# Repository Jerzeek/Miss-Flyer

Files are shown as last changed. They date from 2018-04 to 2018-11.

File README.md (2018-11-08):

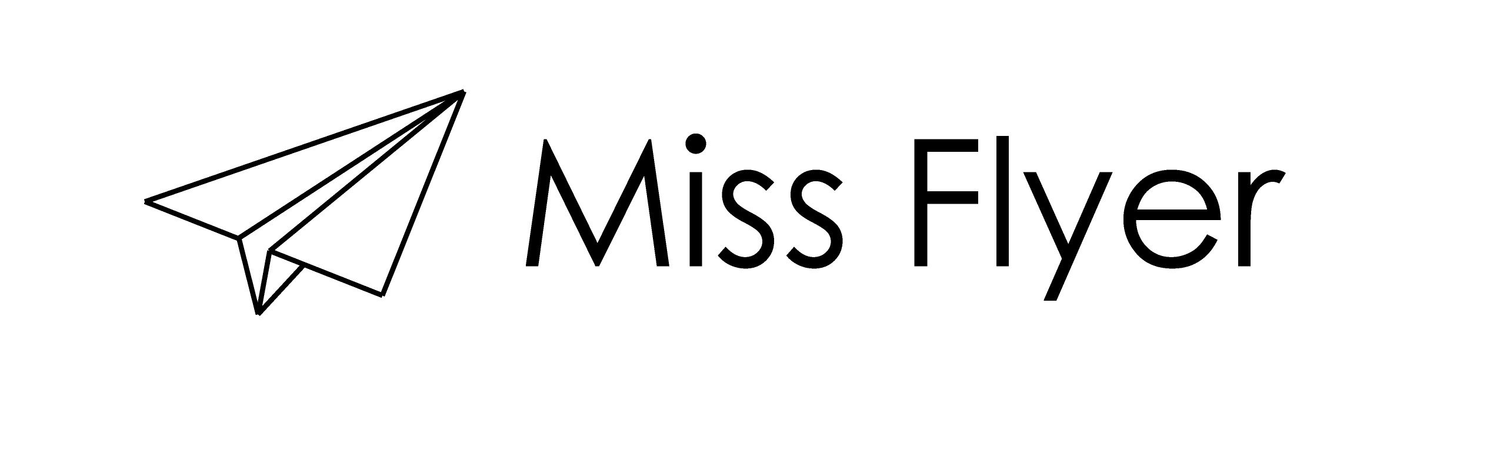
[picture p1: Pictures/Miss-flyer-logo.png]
Project logo

***
Miss Flyer the best use of a misprint!
It can turn an ordenairy paper into an extra ordaniary paper plane with only one swipe! :open_mouth:

Entirely made from one single sheet of lasercutted plywood.

KRO-NCRV, Klaas vindt uit (Dutch TV) seemed to like it, so they wanted to show it to everyone :smiley:
here is a to the video:
(click on image)
Klaas vindt uit video (https://www.youtube.com/watch?v=qRwEvvZekd8)

One gif says more than 1000 words:
Gif

Miss Flyer in use:
Demo photo

Overview photo:
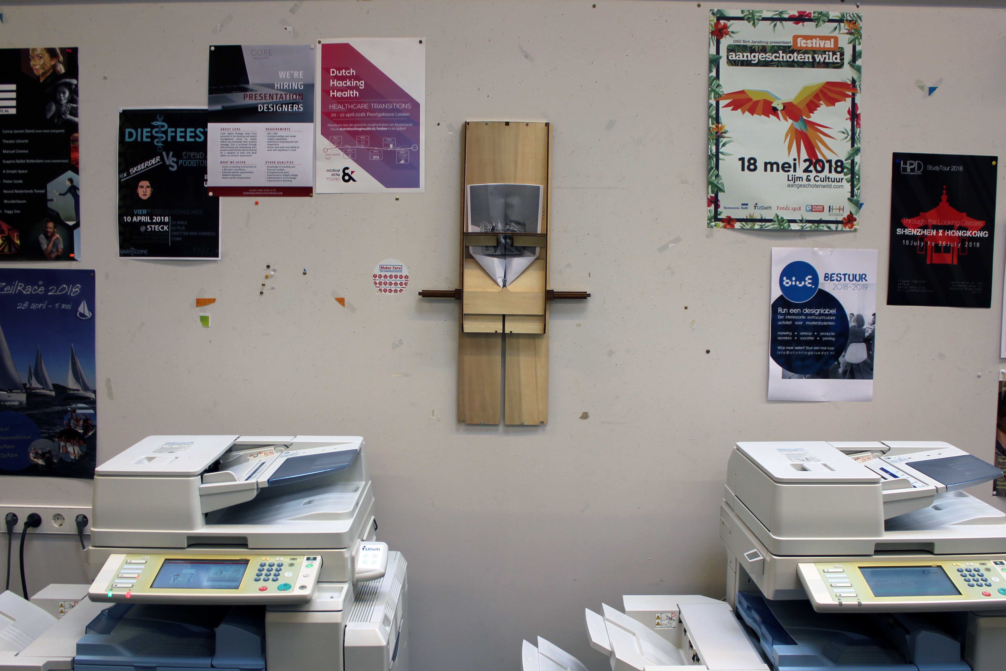
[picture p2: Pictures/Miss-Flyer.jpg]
overview


Lasercut overview:
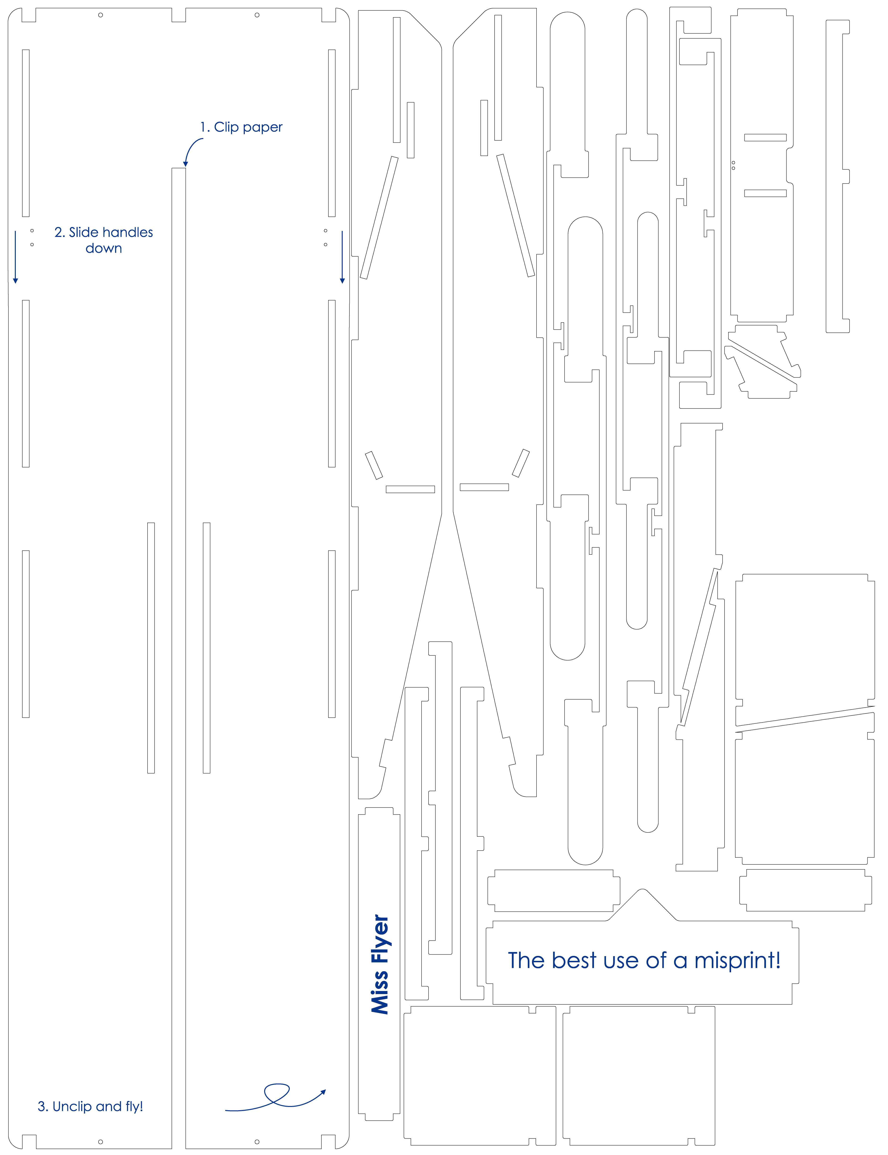
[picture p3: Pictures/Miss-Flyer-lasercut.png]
Lasercut photo


Initial sketch:
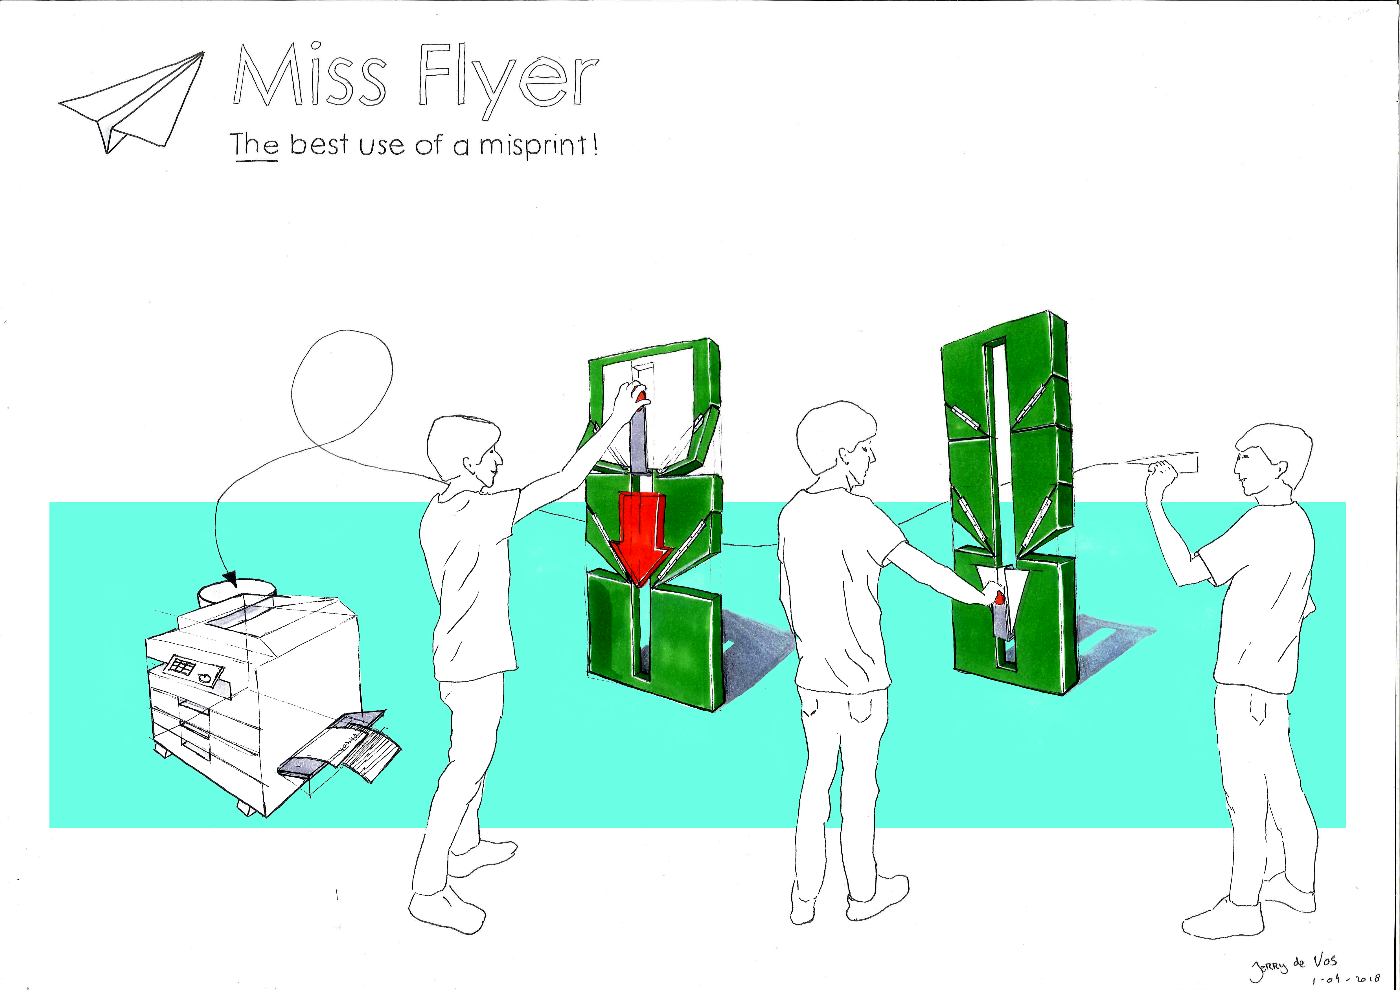
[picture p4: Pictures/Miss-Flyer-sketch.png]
Initial sketch


How i made all of this? I kept a A3 logbook:
logbook

***
Video:
(click on image)
Miss Flyer Video (https://www.youtube.com/watch?v=A3kHtu0t324)

***
Bill Of Material:

|Quantity|Description|Dimentions|
|---|---|---|
|1|Sheet of plywood|5mm 830x650mm|
|1|Fishing rod or other thin wire|40cm|
|1|Binder clip|20mm(smaller=better)|
|1|Rubber|20x10mm|

***

Instructions:
1. Assemble subassembly 1:
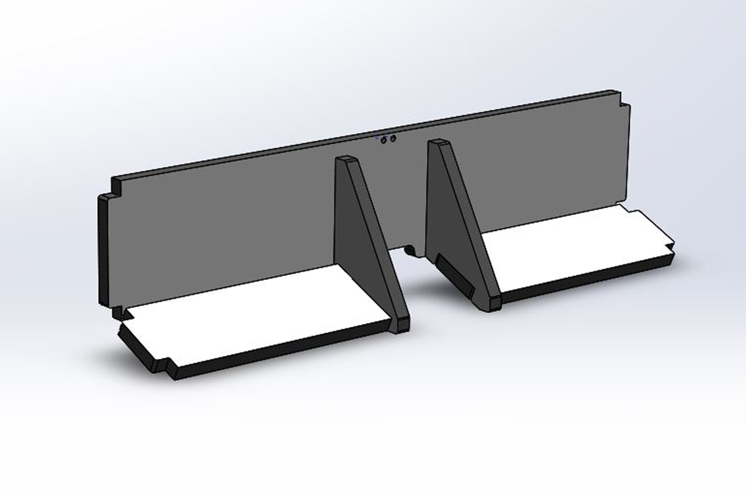
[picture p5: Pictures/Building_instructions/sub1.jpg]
Step 1


2. Assemble subassembly 2:
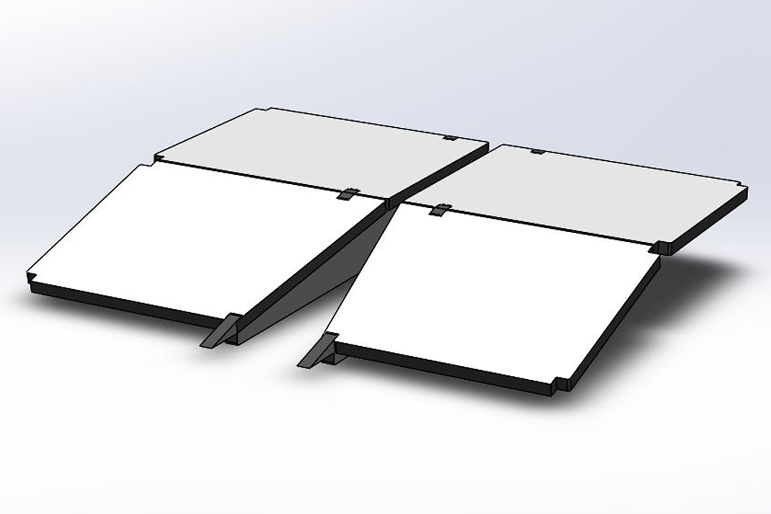
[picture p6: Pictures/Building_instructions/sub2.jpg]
Step 2


3. Glue slider together:
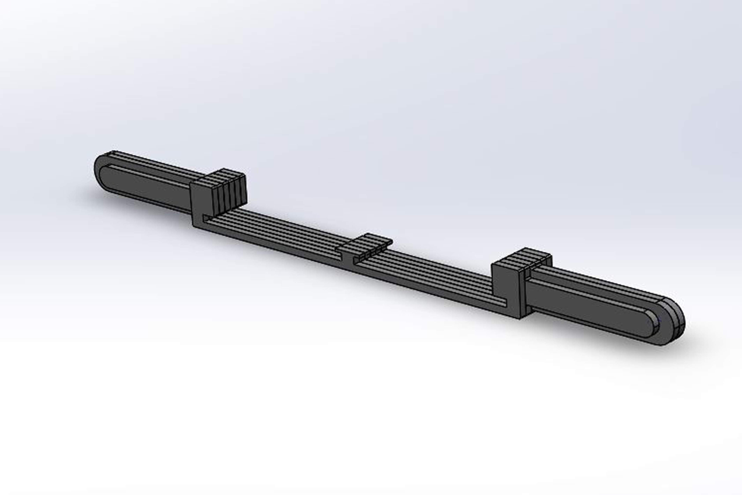
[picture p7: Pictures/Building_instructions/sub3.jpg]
Step 3


4. Insert slider and add endstops:
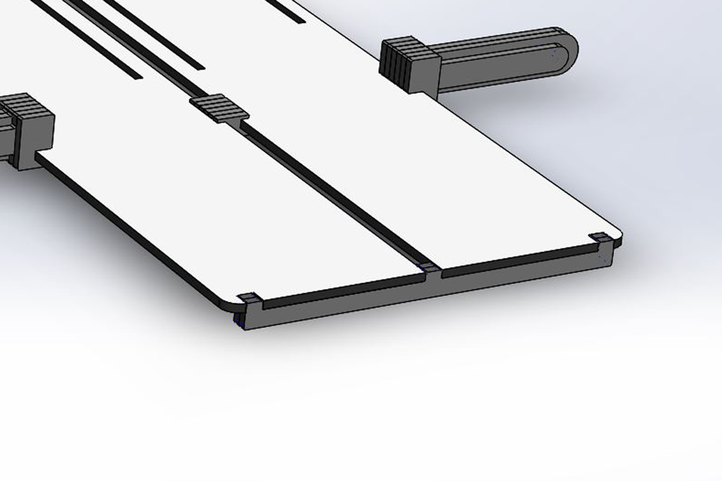
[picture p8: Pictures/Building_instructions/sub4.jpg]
Step 4


5. Assemble rest:
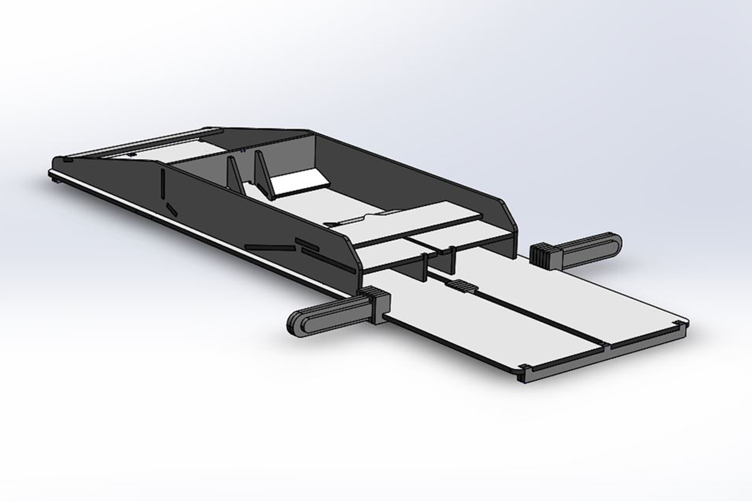
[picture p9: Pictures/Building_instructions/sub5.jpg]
Step 5


6. Cutout wood between holes so wire can sit flush and slider can still slide:
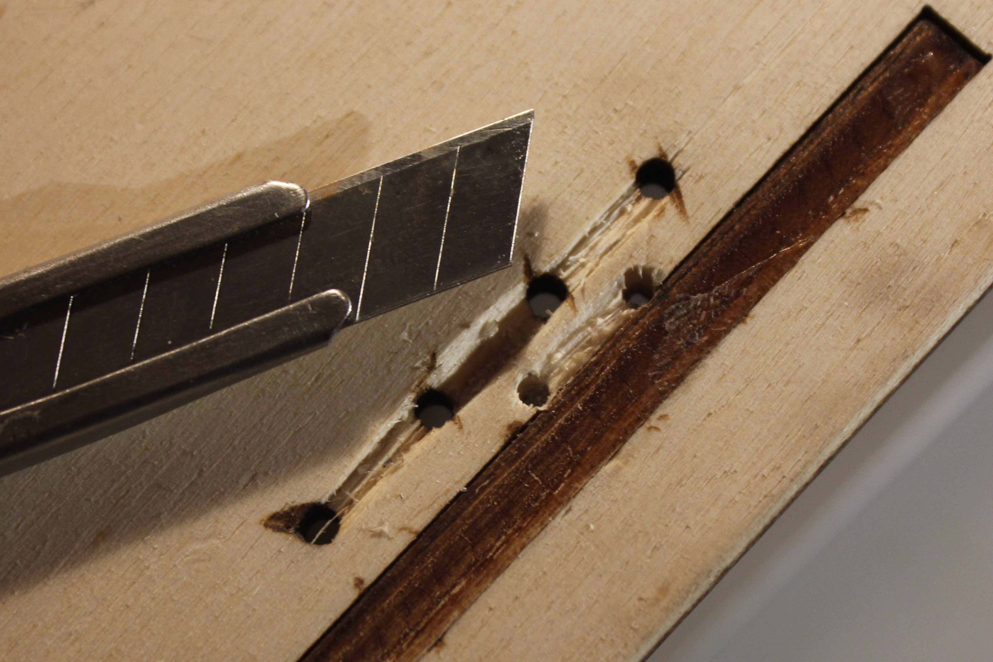
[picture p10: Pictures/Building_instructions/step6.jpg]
Step 6


7. Glue or bolt clip down and add a piece of rubber (in my case bike tire) to the clip for better grip:
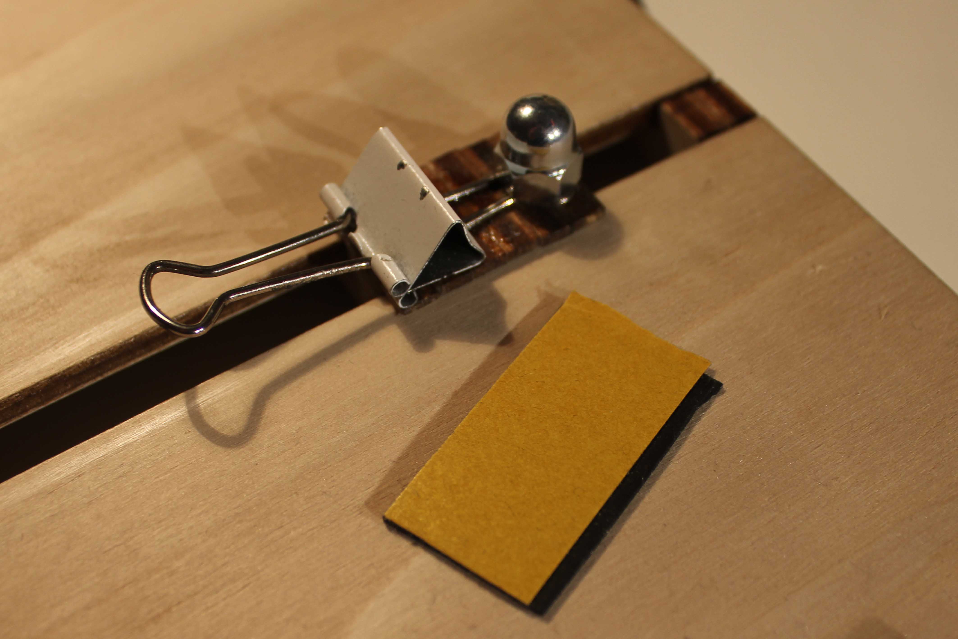
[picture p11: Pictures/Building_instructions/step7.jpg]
Step 7


8. Like this:
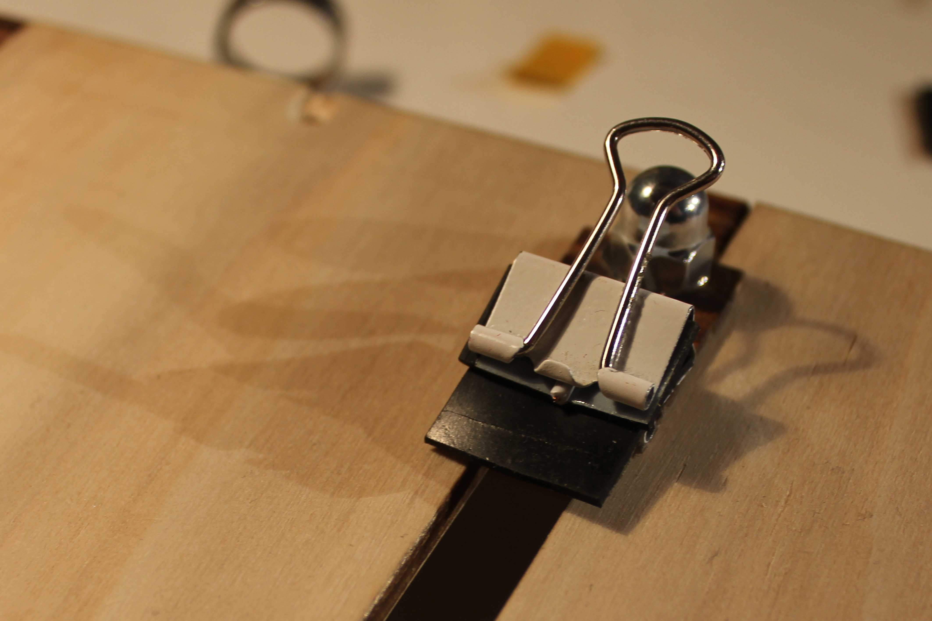
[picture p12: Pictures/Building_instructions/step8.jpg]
Step 8


NOW HAVE FUN!!
***
Changelog:
 - Version 1: Genesis
 - Version 2: Changed gap from 5mm to 3mm, changed distance between step 1 and 2 from 120 mm to 140 mm
 - Version 3: Zohar & me made the second version but this raised some issues. changed gap back to 5mm again cause the paper kept ripping. changed the cutouts to 4.95mm so it's more of a friction fit.
***
Future development:
 - [x] Write building Instructions
 - [x] Better performance
 - [x] Engraving
 - [ ] No need for glue
 - [ ] More paper plane designs
 - [x] Have a paper plane war at the office!

***
Open Source Hardware

It's Open Source, go ahead build it!

Made for PO2 Project at the Technical university of Delft.
for questions please feel open in issue [here](https://github.com/Jerzeek/Miss-Flyer/issues) or

send me an email (info @ jerrydevos.nl)

The paper plane folder isn't perfect, sometimes the paper creases. let me know if you have improvements :smiley:



***

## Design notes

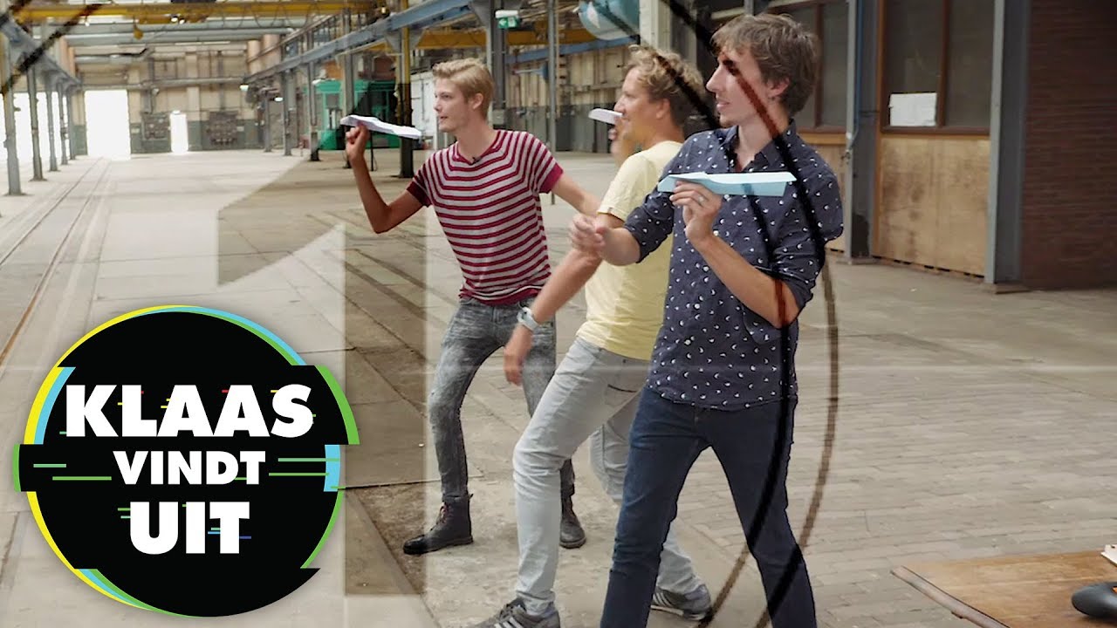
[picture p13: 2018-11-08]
Pictures/Miss-Flyer-Klaasvindtuit.jpg

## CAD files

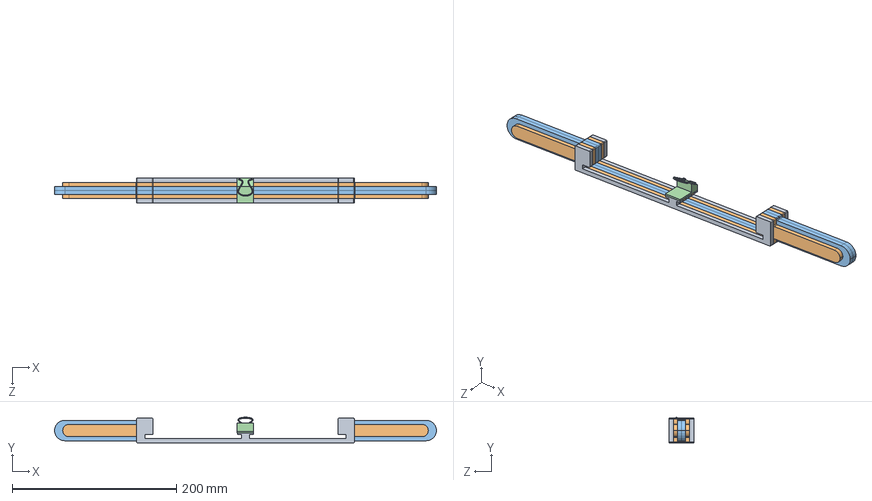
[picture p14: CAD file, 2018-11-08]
CAD_files/Backup of slider2.SLDASM
465.2 x 31.3 x 30.0 mm
slider2-1 x 2
slider2-2 x 2
slider2-3 x 2
clip2

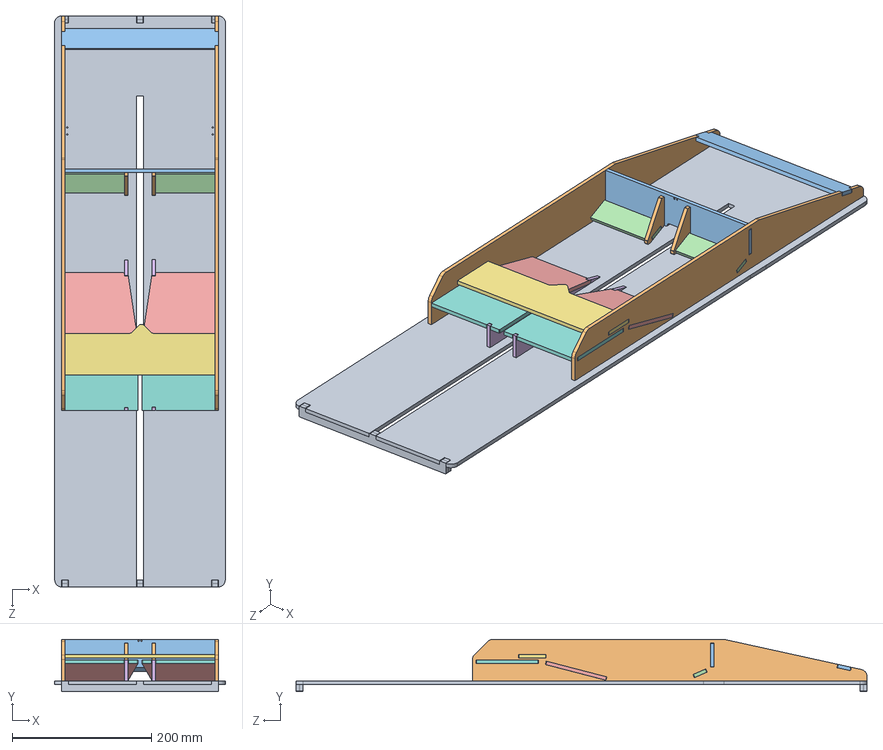
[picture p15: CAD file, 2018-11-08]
CAD_files/frame.SLDASM
245.6 x 75.0 x 820.0 mm
backplate
side x 2
frame-folder
frame-folder2 x 2
frame-secondfold x 2
frame-secondfold3 x 2
frame-secondfold1
frame-secondfold4 x 2
stopper x 4
frame-folder4 x 2
frame-paperholder

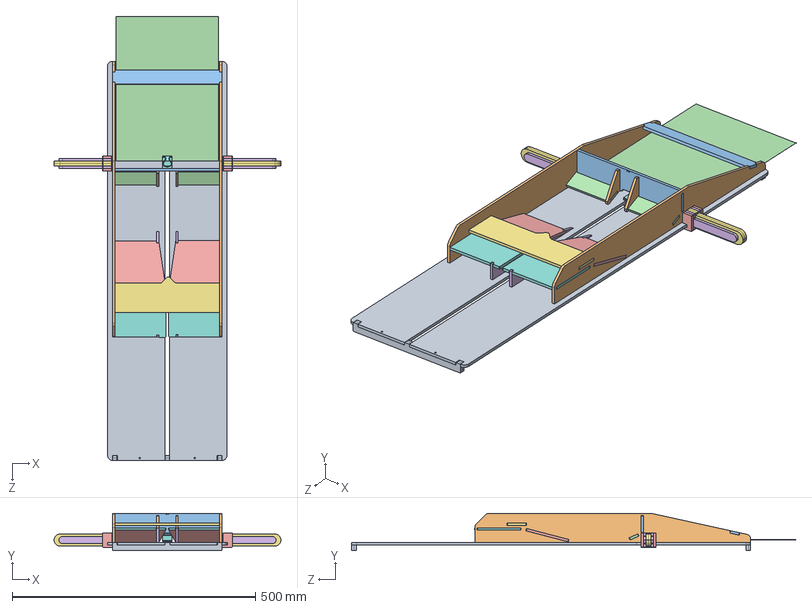
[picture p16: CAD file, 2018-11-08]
CAD_files/assembly plane folder.SLDASM
466.0 x 77.0 x 912.0 mm
backplate
side x 2
frame-folder
frame-folder2 x 2
frame-secondfold x 2
frame-secondfold3 x 2
frame-secondfold1
frame-secondfold4 x 2
stopper x 4
frame-folder4 x 2
frame-paperholder
slider2-1 x 2
slider2-2 x 2
slider2-3 x 2

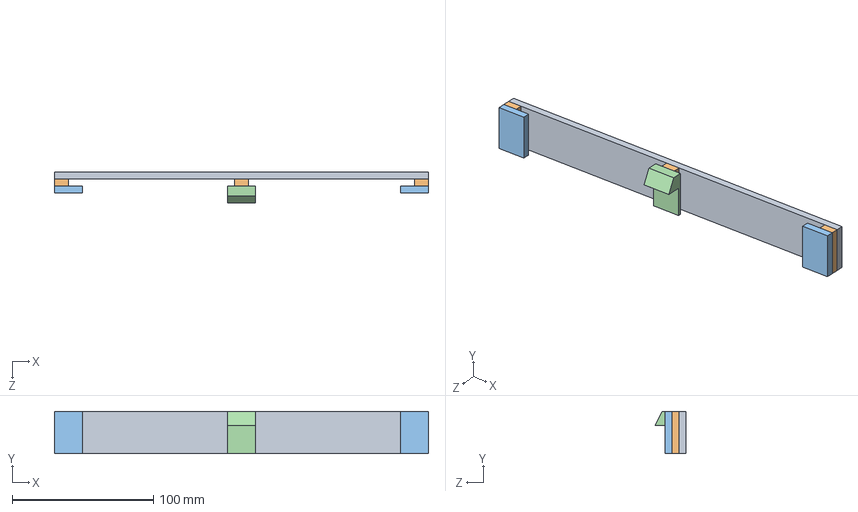
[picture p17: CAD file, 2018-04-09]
CAD_files/slider.SLDASM
265.0 x 30.0 x 22.0 mm
slider back
slider middle x 3
slider top x 2
clip2

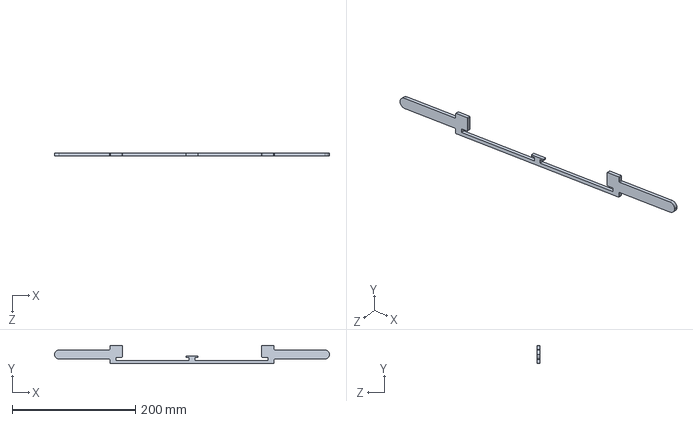
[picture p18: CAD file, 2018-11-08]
CAD_files/Backup of slider2-2.SLDPRT
446.0 x 30.0 x 5.00 mm

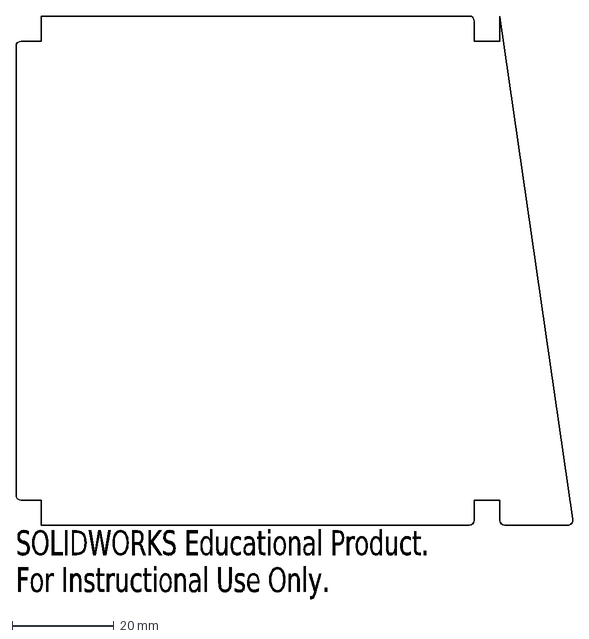
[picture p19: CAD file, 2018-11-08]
CAD_files/DXF/sub2-2 2x.DXF
SOLIDWORKS Educational Product.
For Instructional Use Only.

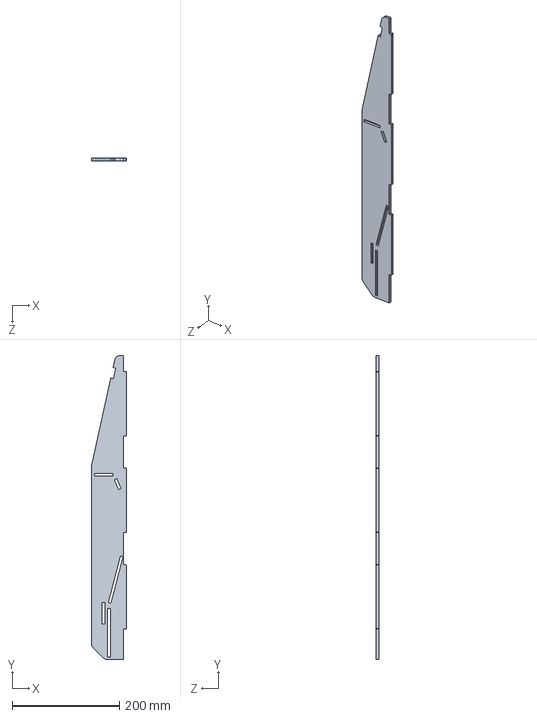
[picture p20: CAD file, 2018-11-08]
CAD_files/Backup of side.SLDPRT
65.0 x 566.8 x 5.00 mm

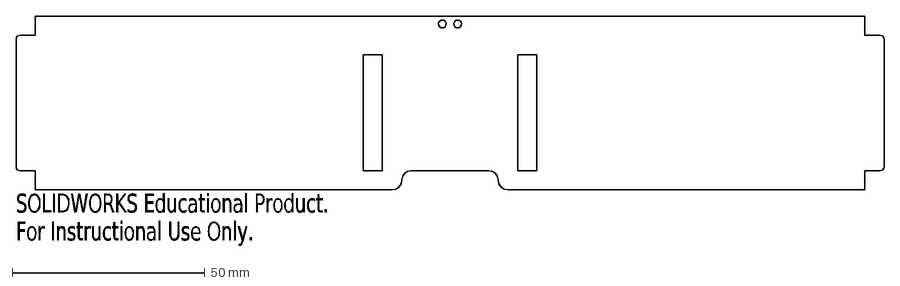
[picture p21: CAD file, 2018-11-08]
CAD_files/DXF/sub1-1 1x.DXF
SOLIDWORKS Educational Product.
For Instructional Use Only.

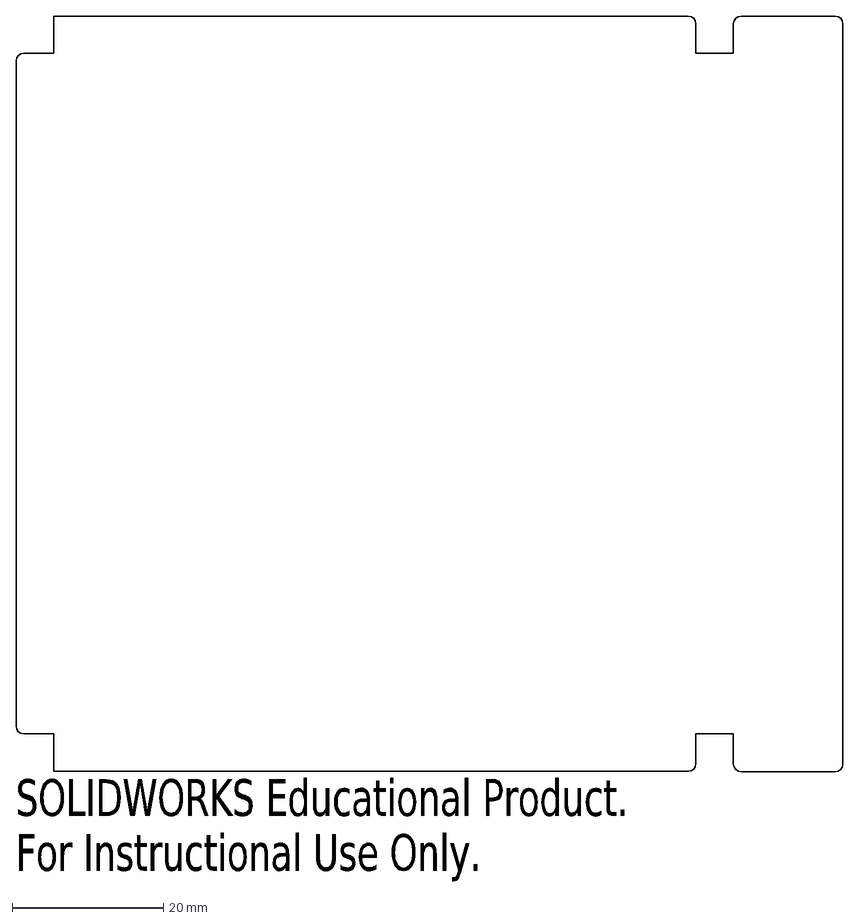
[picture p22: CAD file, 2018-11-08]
CAD_files/DXF/sub2-1 2x.DXF
SOLIDWORKS Educational Product.
For Instructional Use Only.

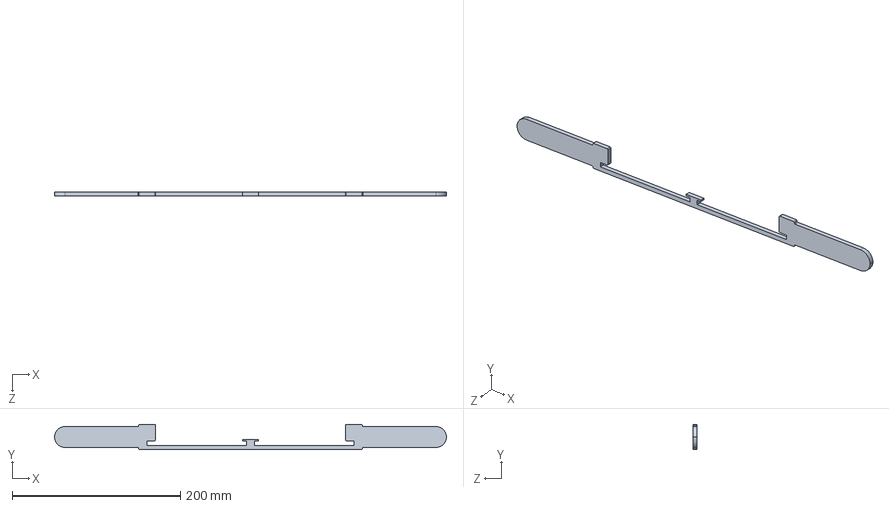
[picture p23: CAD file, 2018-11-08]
CAD_files/Backup of slider2-3.SLDPRT
466.0 x 30.0 x 5.00 mm

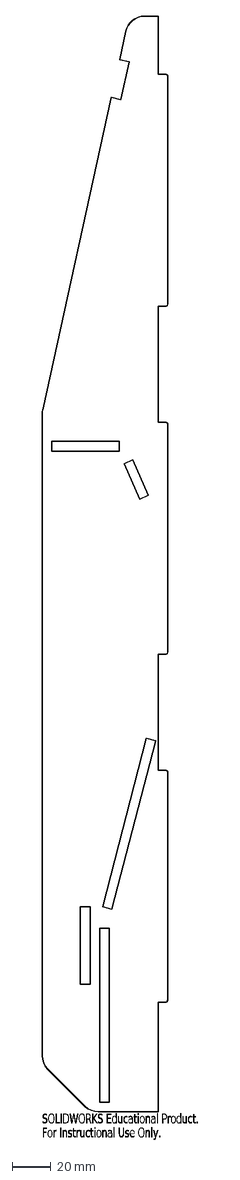
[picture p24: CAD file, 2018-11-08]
CAD_files/DXF/sub5-2 2x.DXF
SOLIDWORKS Educational Product.
For Instructional Use Only.

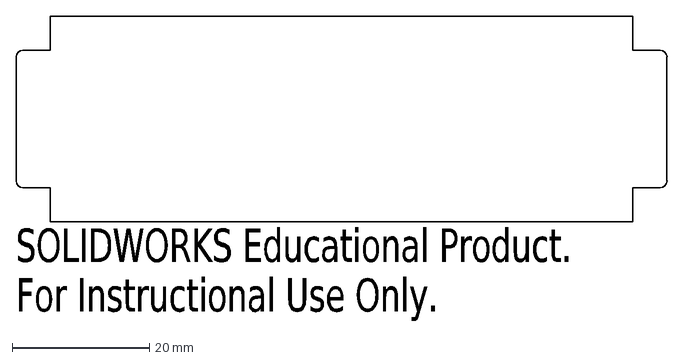
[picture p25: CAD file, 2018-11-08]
CAD_files/DXF/sub1-2 2x.DXF
SOLIDWORKS Educational Product.
For Instructional Use Only.

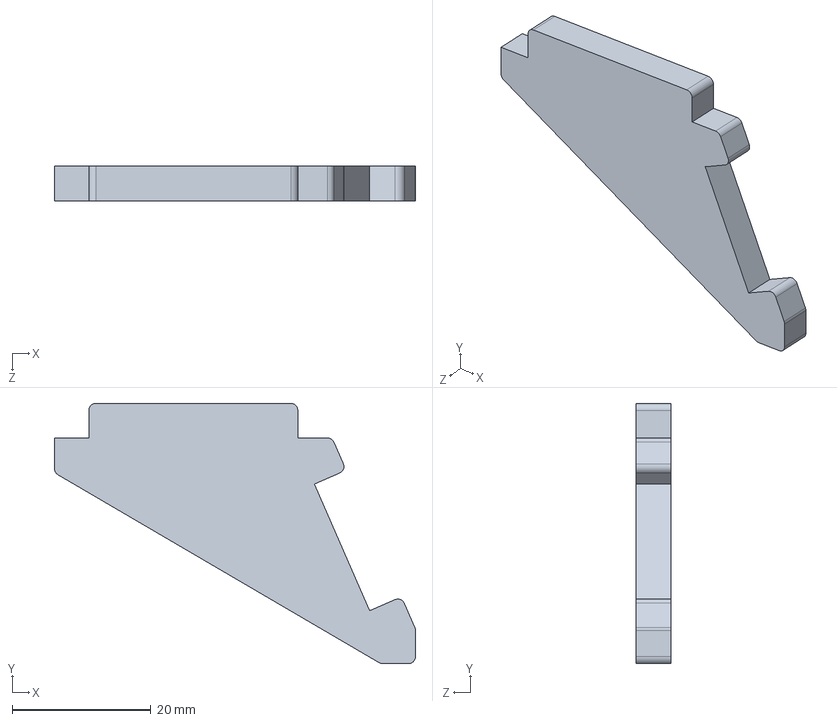
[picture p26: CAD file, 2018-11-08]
CAD_files/frame-folder4.SLDPRT
52.0 x 37.5 x 5.00 mm

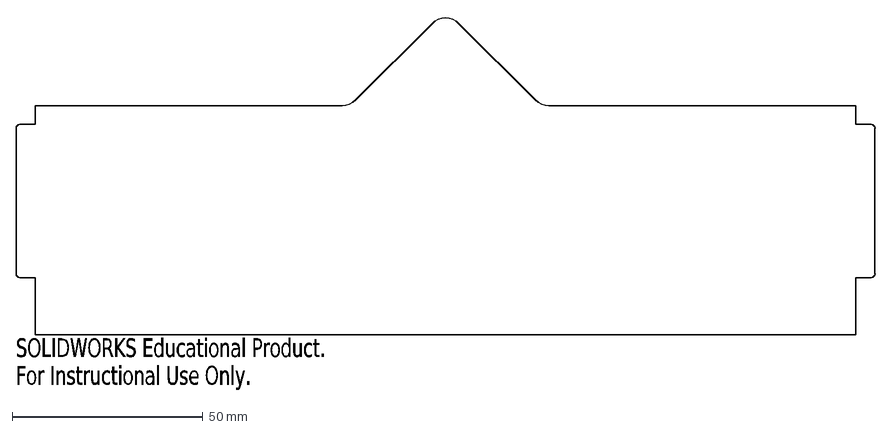
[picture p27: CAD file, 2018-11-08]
CAD_files/DXF/sub5-3 1x.DXF
SOLIDWORKS Educational Product.
For Instructional Use Only.

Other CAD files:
CAD_files/Backup of frame.SLDASM
CAD_files/Backup of assembly plane folder.SLDASM
CAD_files/slider2.SLDASM
CAD_files/stopper.SLDPRT
CAD_files/A4 paper.SLDPRT
CAD_files/Backup of backplate.SLDPRT
CAD_files/Backup of frame-folder4.SLDPRT
CAD_files/Backup of frame-secondfold1.SLDPRT
CAD_files/Backup of slider2-1.SLDPRT
CAD_files/DXF/sub1-3 2x.DXF
CAD_files/DXF/sub2-3 2x.DXF
CAD_files/DXF/sub3-1 2x.DXF
CAD_files/DXF/sub3-2 2x.DXF
CAD_files/DXF/sub3-3 2x.DXF
CAD_files/DXF/sub4-1 4x.DXF
CAD_files/DXF/sub4-2 1x.DXF
CAD_files/DXF/sub5-1 1x.DXF
CAD_files/backplate.SLDPRT
CAD_files/clip.SLDPRT
CAD_files/clip1.SLDPRT
CAD_files/clip2.SLDPRT
CAD_files/frame-folder.SLDPRT
CAD_files/frame-folder2.SLDPRT
CAD_files/frame-folder3.SLDPRT
CAD_files/frame-paperholder.SLDPRT
CAD_files/frame-secondfold.SLDPRT
CAD_files/frame-secondfold1.SLDPRT
CAD_files/frame-secondfold3.SLDPRT
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

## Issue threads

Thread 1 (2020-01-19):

Incomplete instructions

lkdurvin, 2020-01-19:
The instructions have a step for making a groove for a wire, but there is no step describing the wire or its placement. There is no wire in any photos. The bill of materials lists it:

1 | Fishing rod or other thin wire | 40cm

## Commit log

2018-04-08 Captial letter CAD render
2018-04-09 Added CAD files
    Added SolidWorks CAD files for reference
    [A4 paper.SLDPRT, assembly plane folder.SLDASM, backplate.SLDPRT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]
2018-04-18 version 2!!
    redesign, improved performance,
    building instructions,
    video and photo's of product in use.
    [A4 paper.SLDPRT, assembly plane folder.SLDASM, backplate.SLDPRT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]
2018-11-08 Version 3: Improved after test at Klass Vindt Uit
    Improved the flyer again,
    Added picture/video of Klaas Vindt Uit
    [Backup of assembly plane folder.SLDASM, Backup of backplate.SLDPRT, Backup of frame-folder4.SLDPRT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]

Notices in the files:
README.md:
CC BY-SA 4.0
